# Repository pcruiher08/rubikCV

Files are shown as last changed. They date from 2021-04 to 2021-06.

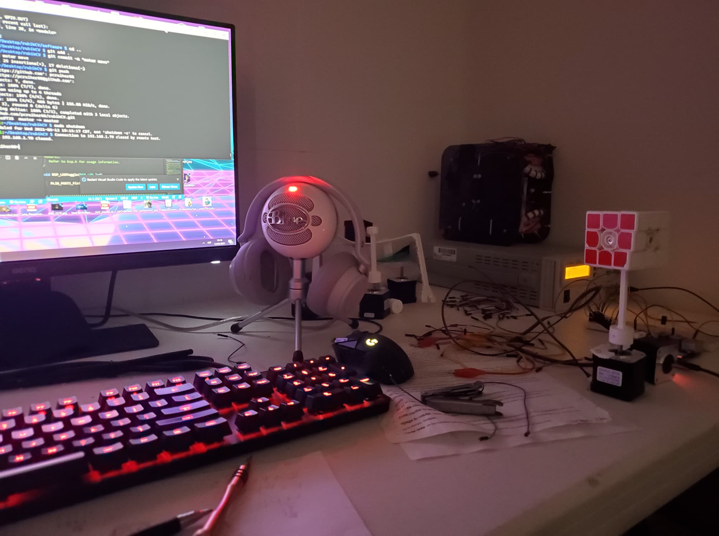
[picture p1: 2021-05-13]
journal/Day4.jpg

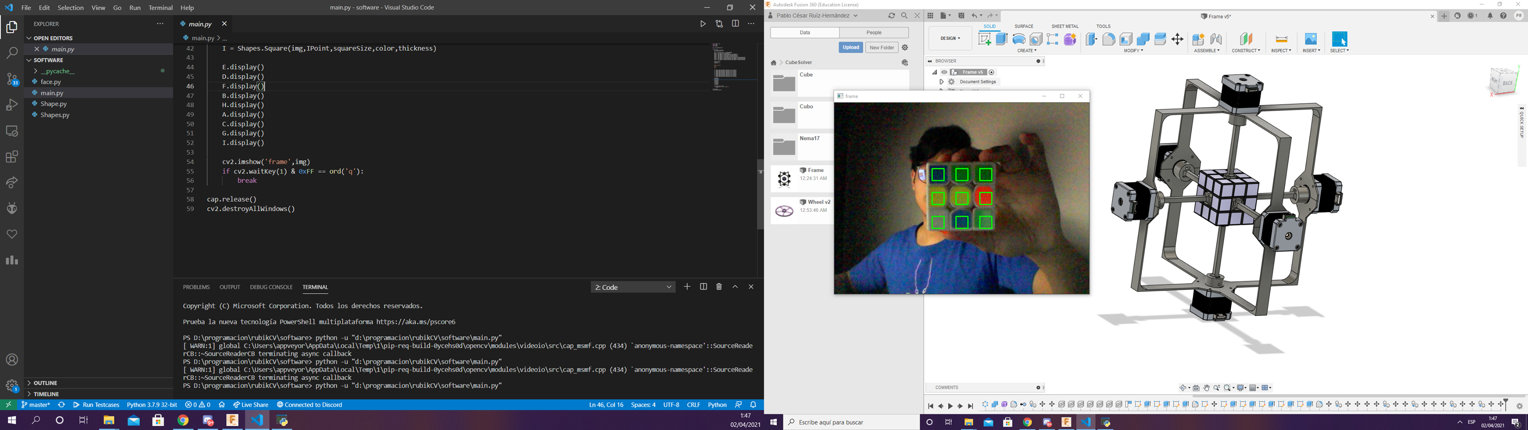
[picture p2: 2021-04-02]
journal/ssDay1.png

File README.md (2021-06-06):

# rubikCV

## Objectives

## Approach

## Development

### Mechanics
#### Brief discussion about motors
#### MoYu Weilong gts v2
#### First design (unreliable)
#### Second design (screenshots and video)
#### Screw joint design
#### Motor-Cube joints
#### 3D printing and laser cutting

### Electronics
#### Controller decision (raspberry)
#### A4988 Motor driver
#### LCD
#### 18650 lithium batteries
#### LEDs
#### Arduino with LEDs and how it would be implemented on the raspberry (level shifter)
#### Brief disccussion about the pcb and the breadboard
#### WebCam

### Software

#### OpenCV justification
* Image processing (5 pictures per face)
* Arucos (Augmented reality and geometry functions)
* HSV
* Dominant Color algorithm
#### Cube map (diagrams, polygon class)
#### States machine (scanning phase with pre defined movements)
#### Kociemba
#### Motor movement (parser, motor class, motor speed)
#### LEDs
#### LCD (LCD class)

## Results

## Improvements

## Conlusions

## DIY

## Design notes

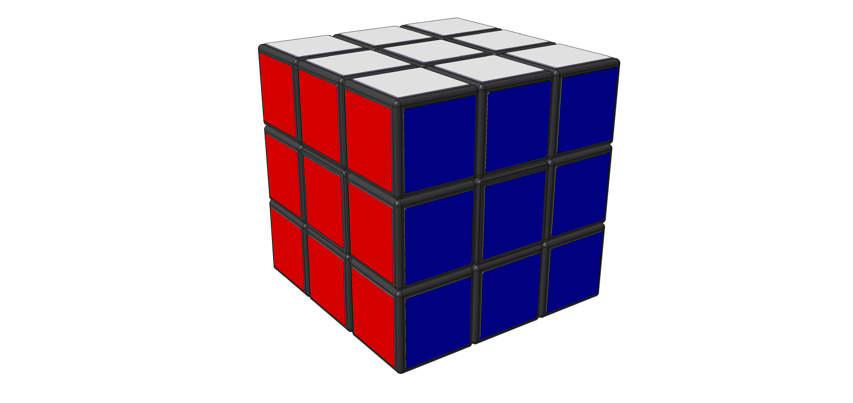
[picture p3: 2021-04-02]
hardware/CAD/cube/RubiksCube.jpg

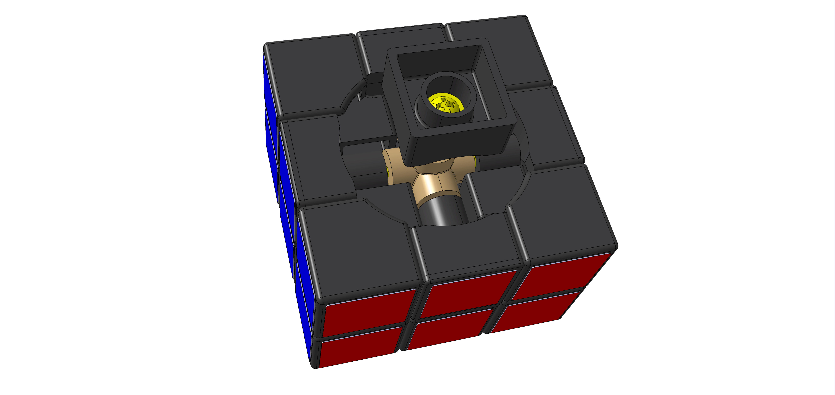
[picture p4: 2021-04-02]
hardware/CAD/cube/RubiksCube2.jpg

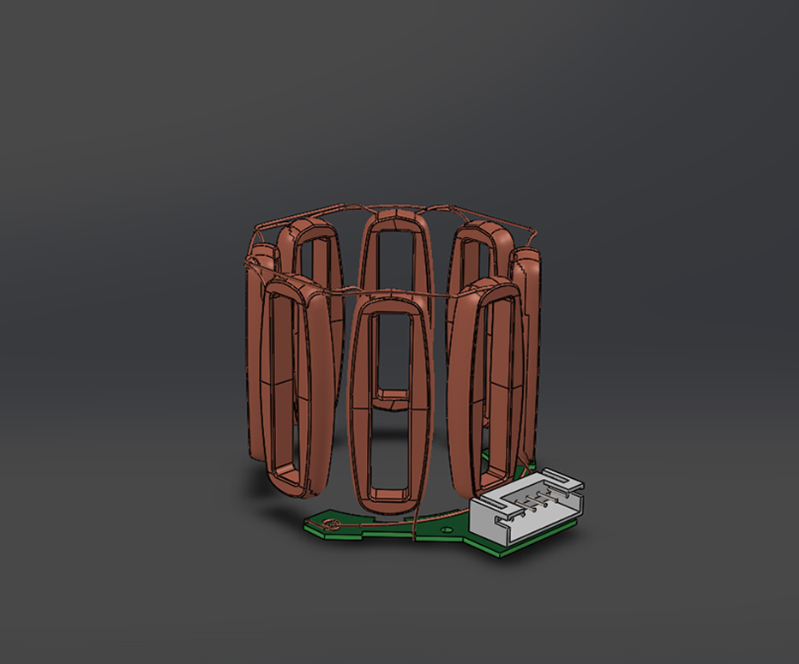
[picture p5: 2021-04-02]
hardware/CAD/nema17/Electronics.jpg

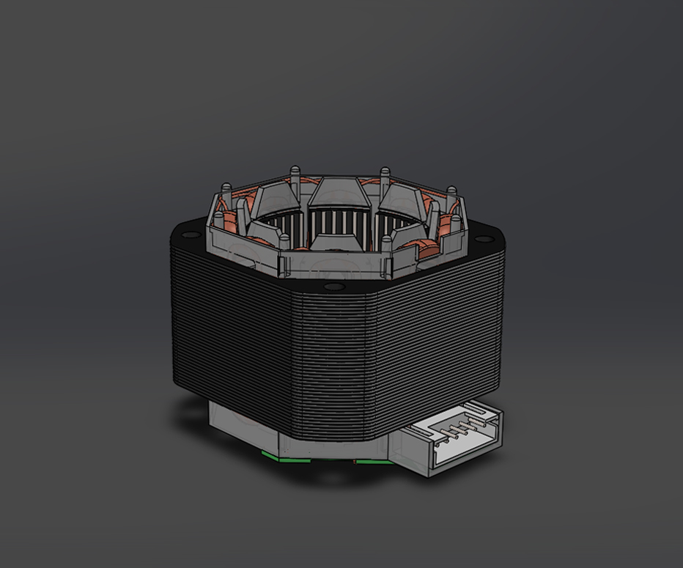
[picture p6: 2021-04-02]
hardware/CAD/nema17/Stator.jpg

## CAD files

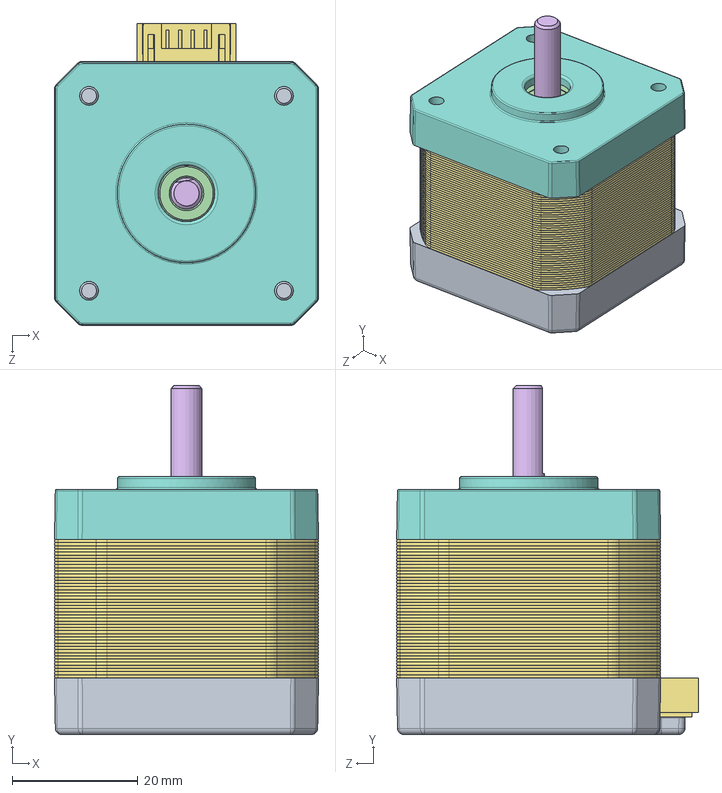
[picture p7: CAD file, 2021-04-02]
hardware/CAD/nema17/Nema17.SLDASM
42.0 x 55.5 x 48.0 mm
Bottom_cap
Protective_film_bottom
Bearing_spring
Bearing x 2
Thick_washer x 2
Rotor
Stator
Top_cap
Screw x 4

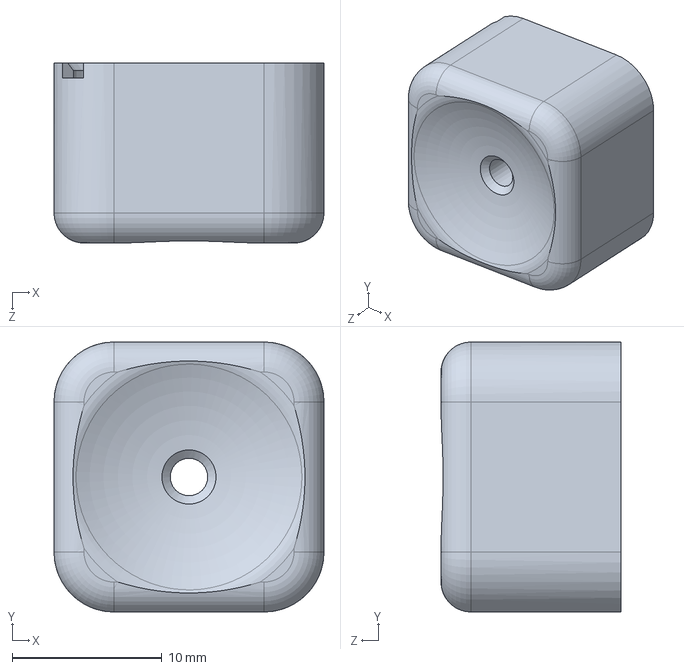
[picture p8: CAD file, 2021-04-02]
hardware/CAD/3x3 mk1/centre.SLDPRT
18.0 x 18.0 x 12.0 mm

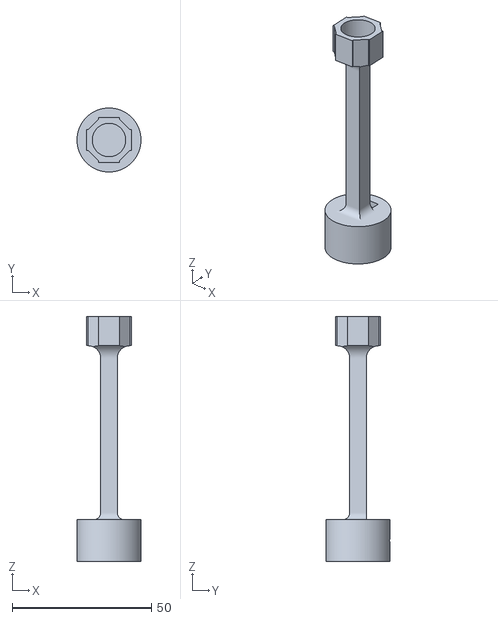
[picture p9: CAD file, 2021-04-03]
hardware/CAD/Body12.stl
23.0 x 23.0 x 88.0

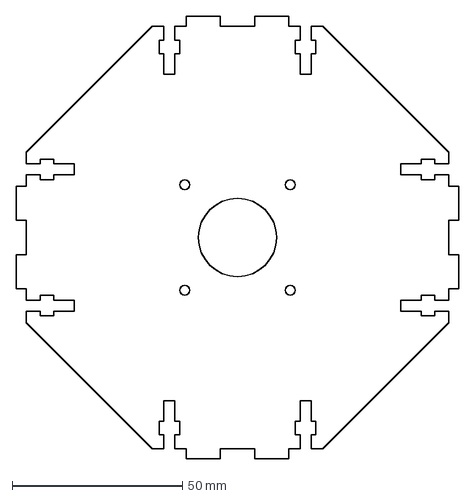
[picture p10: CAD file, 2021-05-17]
hardware/CAD/Corte Laser/tapa.dxf
130.0 x 130.0 mm

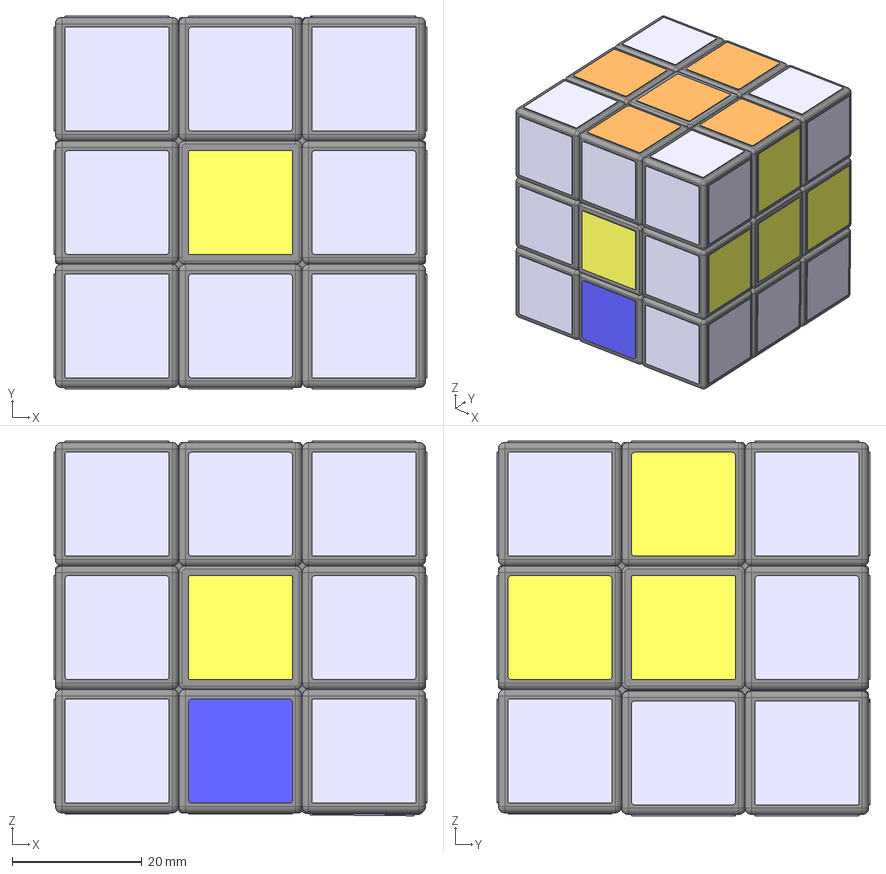
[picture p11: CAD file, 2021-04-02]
hardware/CAD/cube/RubiksCube.stp
57.4 x 57.4 x 57.7 mm
Cross
Center x 6
Edge x 12
Corner x 8
Cup x 6
Spring x 6
Coloring

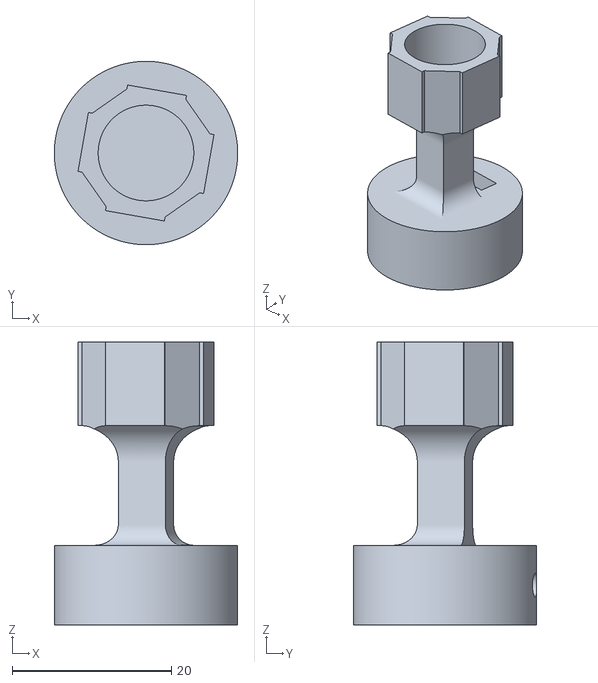
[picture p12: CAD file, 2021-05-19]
hardware/CAD/Impresion 3D/jointv1.stl
23.0 x 23.0 x 35.5

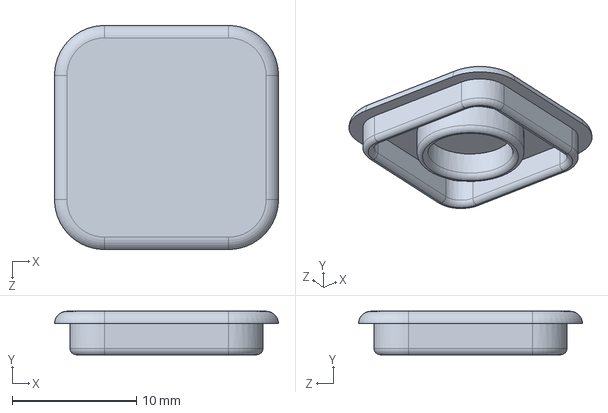
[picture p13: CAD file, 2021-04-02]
hardware/CAD/3x3 mk1/Cap.SLDPRT
18.0 x 3.50 x 18.0 mm

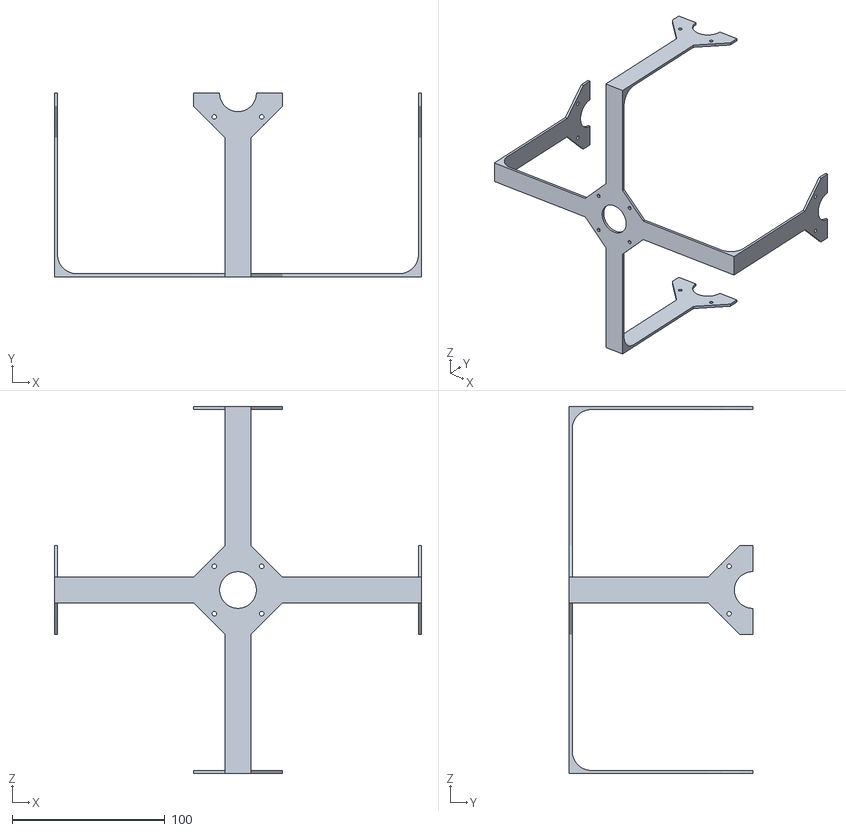
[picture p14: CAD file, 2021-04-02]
hardware/CAD/Body2.stl
240.0 x 120.0 x 240.0

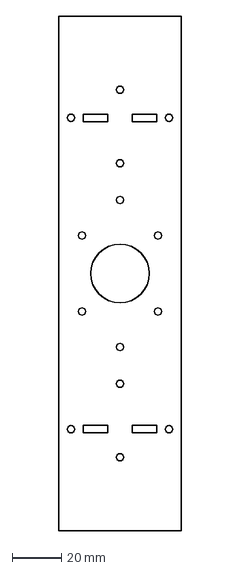
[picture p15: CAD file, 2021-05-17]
hardware/CAD/Corte Laser/columna.dxf
50.0 x 210.0 mm

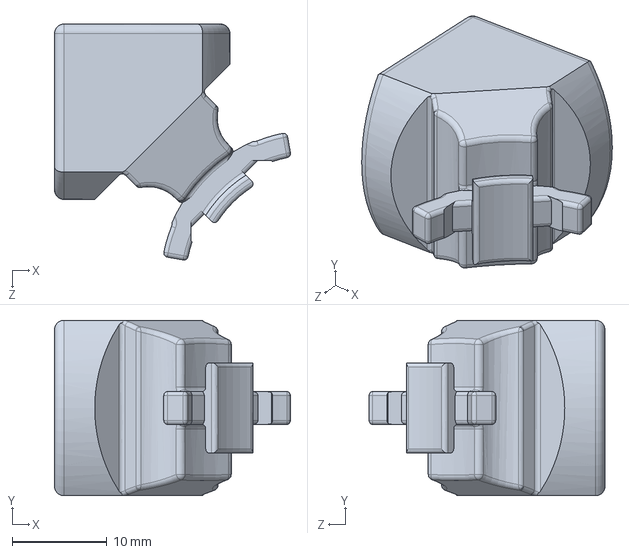
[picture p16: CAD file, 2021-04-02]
hardware/CAD/3x3 mk1/Edge.SLDPRT
24.9 x 18.5 x 24.9 mm

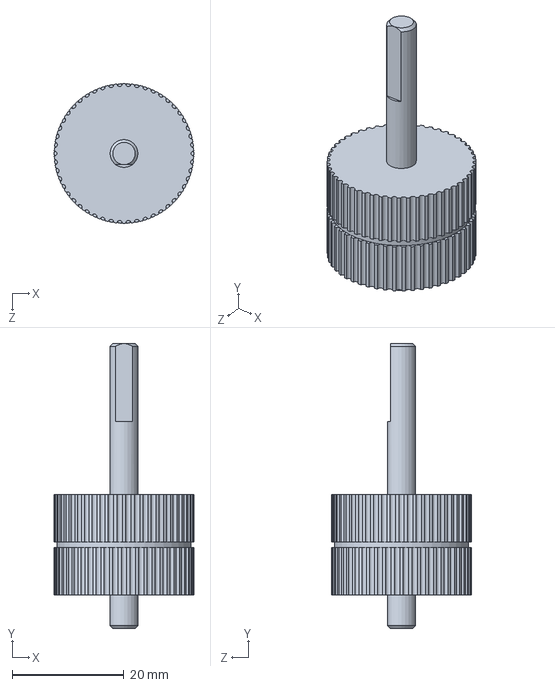
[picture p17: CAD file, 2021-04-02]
hardware/CAD/nema17/Rotor.SLDPRT
25.0 x 51.0 x 25.0 mm

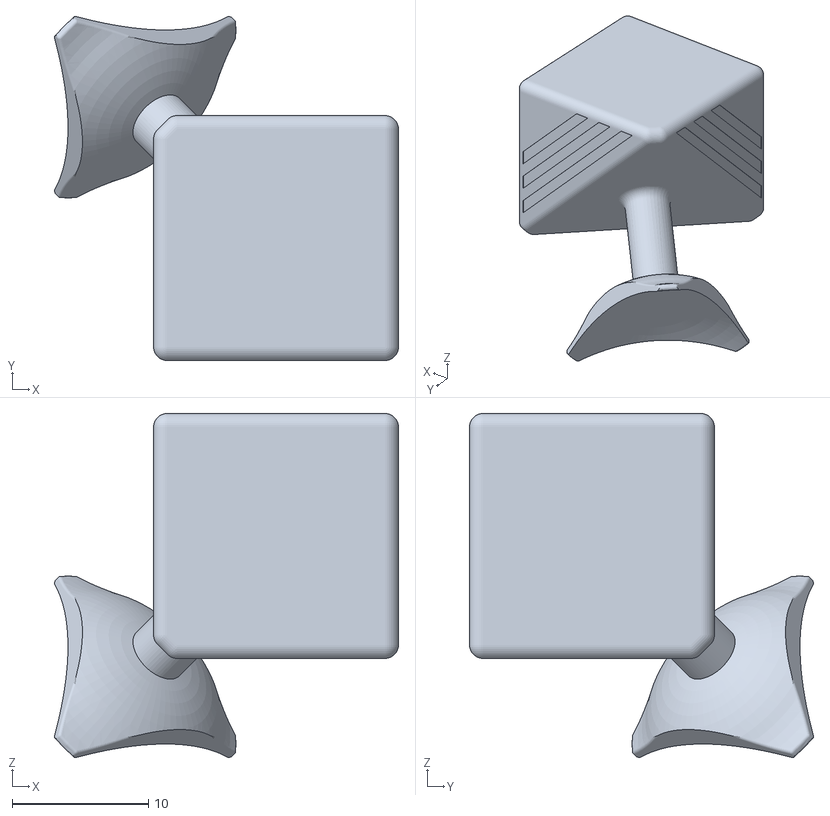
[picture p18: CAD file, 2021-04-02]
hardware/CAD/3x3 mk1/corner.STL
25.3 x 25.3 x 25.3

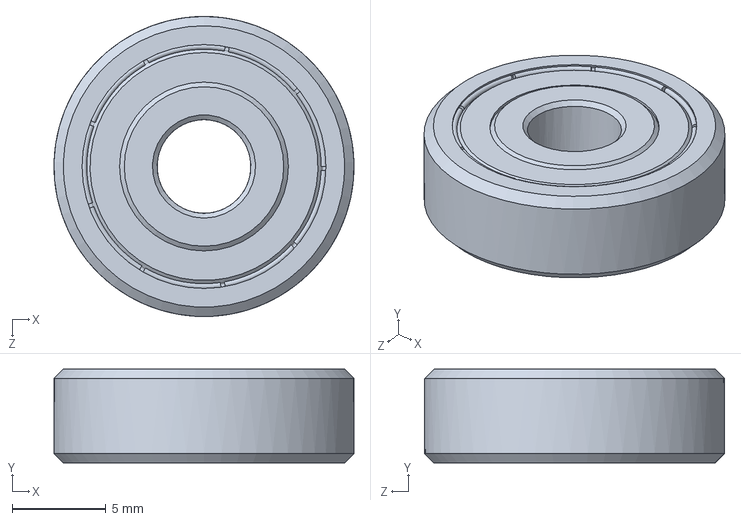
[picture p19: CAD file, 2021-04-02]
hardware/CAD/nema17/Bearing.SLDPRT
16.0 x 5.00 x 16.0 mm

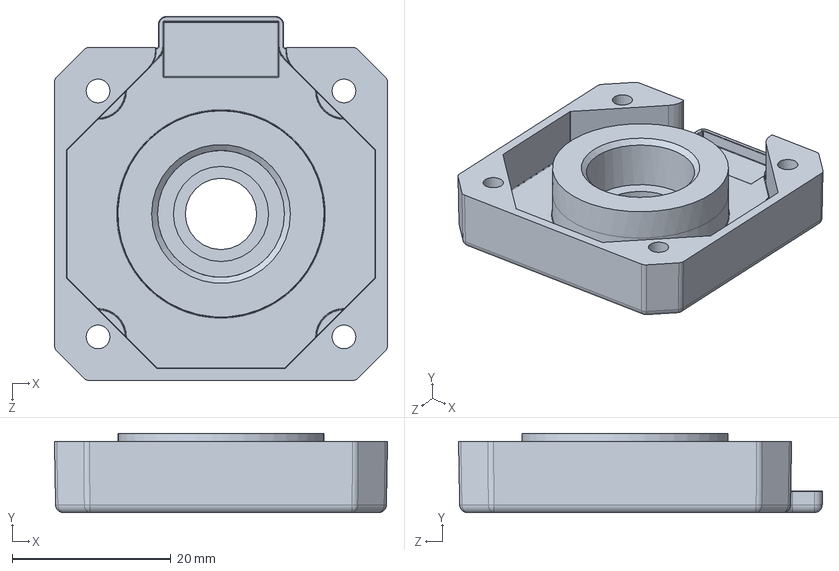
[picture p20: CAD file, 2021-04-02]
hardware/CAD/nema17/Bottom_cap.SLDPRT
42.0 x 10.0 x 45.9 mm

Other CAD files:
hardware/CAD/3x3 mk1/corner post cut.SLDPRT
hardware/CAD/nema17/Bearing_spring.SLDPRT
hardware/CAD/nema17/Top_cap.SLDPRT
hardware/CAD/nema17/Protective_film_bottom.SLDPRT
hardware/CAD/3x3 mk1/Cap.STL
hardware/CAD/3x3 mk1/Edge.STL
hardware/CAD/3x3 mk1/centre.STL
hardware/CAD/nema17/Screw.SLDPRT
hardware/CAD/nema17/Thick_washer.SLDPRT

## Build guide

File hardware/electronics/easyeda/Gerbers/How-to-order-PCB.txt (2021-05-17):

How to Order PCB

Please refer to:
https://docs.easyeda.com/en/PCB/Order-PCB

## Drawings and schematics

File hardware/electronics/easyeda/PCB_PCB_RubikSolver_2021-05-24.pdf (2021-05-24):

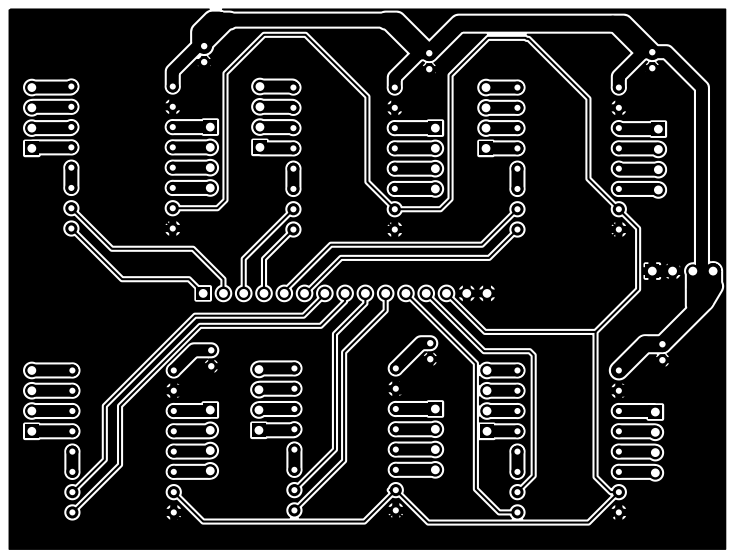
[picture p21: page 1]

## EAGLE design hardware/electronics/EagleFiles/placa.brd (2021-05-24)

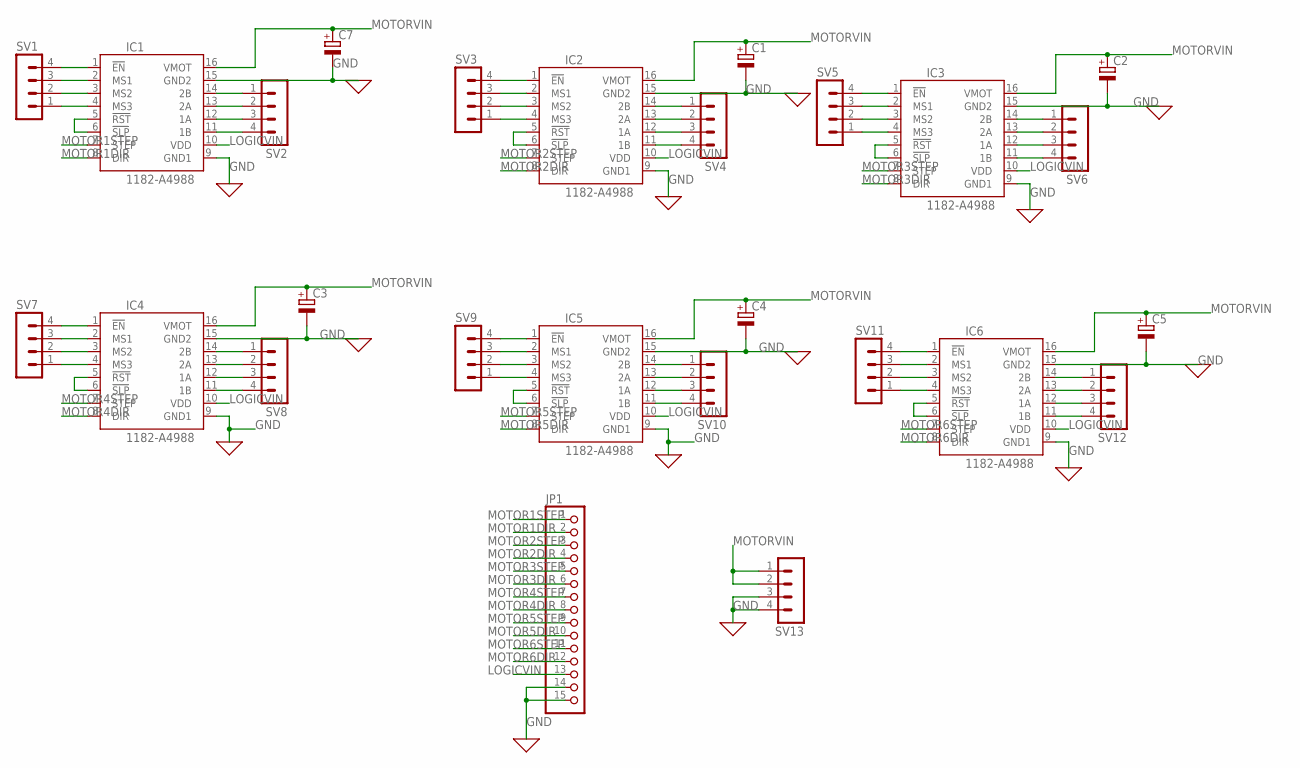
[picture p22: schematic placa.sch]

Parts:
C1, C2, C3, C4, C5, C7: CPOL-EUE2.5-7; E2,5-7
IC1, IC2, IC3, IC4, IC5, IC6: 1182-A4988; A4988
JP1: PINHD-1X15; 1X15
SV1, SV2, SV3, SV4, SV5, SV6, SV7, SV8, SV9, SV10, SV11, SV12, SV13: MA04-1

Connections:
GND: C1.-, C2.-, C3.-, C4.-, C5.-, C7.-, IC1.9 (GND1), IC1.15 (GND2), IC2.9 (GND1), IC2.15 (GND2), IC3.9 (GND1), IC3.15 (GND2), IC4.9 (GND1), IC4.15 (GND2), IC5.9 (GND1), IC5.15 (GND2), IC6.9 (GND1), IC6.15 (GND2), JP1.14, JP1.15, SV13.3, SV13.4
LOGICVIN: IC1.10 (VDD), IC2.10 (VDD), IC3.10 (VDD), IC4.10 (VDD), IC5.10 (VDD), IC6.10 (VDD), JP1.13
MOTOR1DIR: IC1.8 (DIR), JP1.2
MOTOR1STEP: IC1.7 (STEP), JP1.1
MOTOR2DIR: IC2.8 (DIR), JP1.4
MOTOR2STEP: IC2.7 (STEP), JP1.3
MOTOR3DIR: IC3.8 (DIR), JP1.6
MOTOR3STEP: IC3.7 (STEP), JP1.5
MOTOR4DIR: IC4.8 (DIR), JP1.8
MOTOR4STEP: IC4.7 (STEP), JP1.7
MOTOR5DIR: IC5.8 (DIR), JP1.10
MOTOR5STEP: IC5.7 (STEP), JP1.9
MOTOR6DIR: IC6.8 (DIR), JP1.12
MOTOR6STEP: IC6.7 (STEP), JP1.11
MOTORVIN: C1.+, C2.+, C3.+, C4.+, C5.+, C7.+, IC1.16 (VMOT), IC2.16 (VMOT), IC3.16 (VMOT), IC4.16 (VMOT), IC5.16 (VMOT), IC6.16 (VMOT), SV13.1, SV13.2
unnamed: IC1.1 (!EN), SV1.4
unnamed: IC1.2 (MS1), SV1.3
unnamed: IC1.3 (MS2), SV1.2
unnamed: IC1.4 (MS3), SV1.1
unnamed: IC1.5 (!RST), IC1.6 (!SLP)
unnamed: IC2.1 (!EN), SV3.4
unnamed: IC2.2 (MS1), SV3.3
unnamed: IC2.3 (MS2), SV3.2
unnamed: IC1.14 (2B), SV2.1
unnamed: IC1.13 (2A), SV2.2
unnamed: IC1.12 (1A), SV2.3
unnamed: IC1.11 (1B), SV2.4
unnamed: IC2.4 (MS3), SV3.1
unnamed: IC2.5 (!RST), IC2.6 (!SLP)
unnamed: IC2.14 (2B), SV4.1
unnamed: IC2.13 (2A), SV4.2
unnamed: IC2.12 (1A), SV4.3
unnamed: IC2.11 (1B), SV4.4
unnamed: IC3.1 (!EN), SV5.4
unnamed: IC3.2 (MS1), SV5.3
unnamed: IC3.3 (MS2), SV5.2
unnamed: IC3.4 (MS3), SV5.1
unnamed: IC3.5 (!RST), IC3.6 (!SLP)
unnamed: IC3.14 (2B), SV6.1
unnamed: IC3.13 (2A), SV6.2
unnamed: IC3.12 (1A), SV6.3
unnamed: IC3.11 (1B), SV6.4
unnamed: IC4.1 (!EN), SV7.4
unnamed: IC4.2 (MS1), SV7.3
unnamed: IC4.3 (MS2), SV7.2
unnamed: IC4.4 (MS3), SV7.1
unnamed: IC4.5 (!RST), IC4.6 (!SLP)
unnamed: IC4.14 (2B), SV8.1
unnamed: IC4.13 (2A), SV8.2
unnamed: IC4.12 (1A), SV8.3
unnamed: IC4.11 (1B), SV8.4
unnamed: IC5.1 (!EN), SV9.4
unnamed: IC5.2 (MS1), SV9.3
unnamed: IC5.3 (MS2), SV9.2
unnamed: IC5.4 (MS3), SV9.1
unnamed: IC5.5 (!RST), IC5.6 (!SLP)
unnamed: IC5.14 (2B), SV10.1
unnamed: IC5.13 (2A), SV10.2
unnamed: IC5.12 (1A), SV10.3
unnamed: IC5.11 (1B), SV10.4
unnamed: IC6.1 (!EN), SV11.4
unnamed: IC6.2 (MS1), SV11.3
unnamed: IC6.3 (MS2), SV11.2
unnamed: IC6.4 (MS3), SV11.1
unnamed: IC6.5 (!RST), IC6.6 (!SLP)
unnamed: IC6.14 (2B), SV12.1
unnamed: IC6.13 (2A), SV12.2
unnamed: IC6.12 (1A), SV12.3
unnamed: IC6.11 (1B), SV12.4

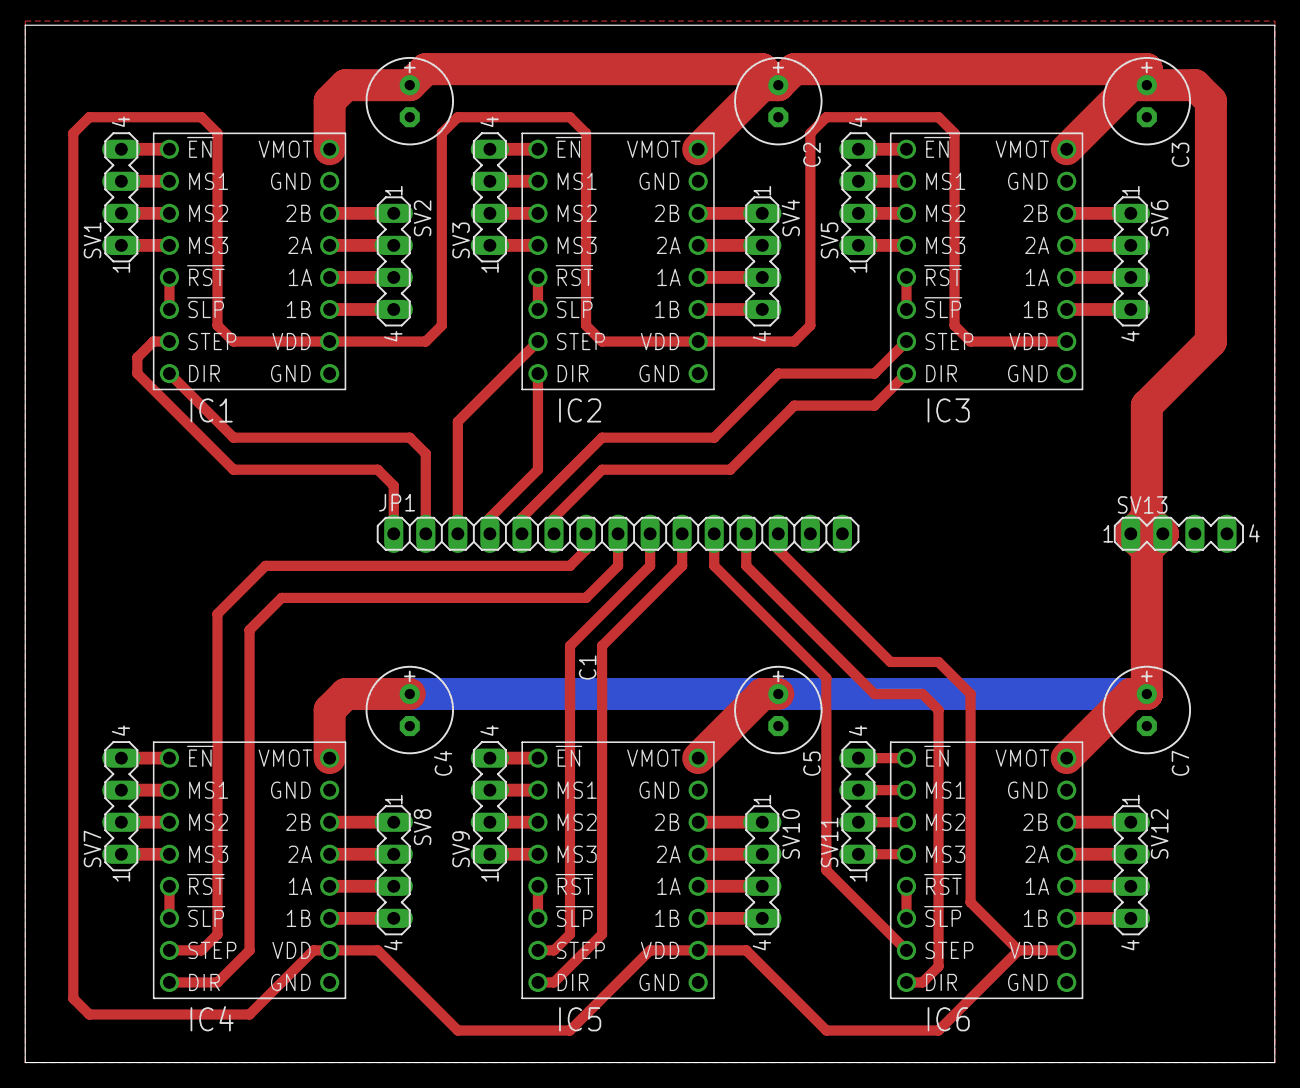
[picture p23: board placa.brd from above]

Board: 2 copper layers, 99.0 x 82.2 mm, 26 parts (0 on the bottom side), 69 nets.

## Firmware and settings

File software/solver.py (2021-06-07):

import cv2
import cv2.aruco as aruco
import numpy as np
import os
from polygon import Polygon 
import math as m 
import LCD
from motor import Motor
import kociemba

def commandParser(series):
    #se recibe un string en formato R U R’ U R U2 R’ U
    movements = series.split(' ')
    for move in movements:
        twoMoves = False
        directionFlag = False
        if len(move) == 2:
            if(move[1] == '2'):
                #cw cw
                twoMoves = True
            else:
                #ccw
                directionFlag = True

        if(move[0] == 'F'):
            if(twoMoves):
                F.turn90CW()
                F.turn90CW()
            else:
                F.turn90(directionFlag)
        if(move[0] == 'L'):
            if(twoMoves):
                L.turn90CW()
                L.turn90CW()
            else:
                L.turn90(directionFlag)  
        if(move[0] == 'R'):
            if(twoMoves):
                R.turn90CW()
                R.turn90CW()
            else:
                R.turn90(directionFlag)
        if(move[0] == 'B'):
            if(twoMoves):
                B.turn90CW()
                B.turn90CW()
            else:
                B.turn90(directionFlag)
        if(move[0] == 'U'):
            if(twoMoves):
                U.turn90CW()
                U.turn90CW()
            else:
                U.turn90(directionFlag)
        if(move[0] == 'D'):
            if(twoMoves):
                D.turn90CW()
                D.turn90CW()
            else:
                D.turn90(directionFlag)
        twoMoves = False
        directionFlag = False


def getMidPoint(a, b):
    return (int((a[0] + b[0]) / 2), int((a[1] + b[1]) / 2))

def getThirdPoint(a, b):
    return (int((a[0] + b[0]) / 3), int((a[1] + b[1]) / 3))

def getTwoThirdsPoint(a, b):
    return (int((a[0] + b[0]) * 2 / 3), int((a[1] + b[1]) * 2 / 3))

def getFractionPoint(a, b, t):
    return ( int(a[0] * (1 - t) ) + int(b[0] * t), int( a[1] * (1 - t) ) + int(b[1] * t) )

def distancePointPoint(a, b):
    return int( m.sqrt( (a[0] - b[0]) * (a[0] - b[0]) + (a[1] - b[1]) * (a[1] - b[1]) ) )

def pointInterceptPointPointPointPoint(a, b, c, d):

    divide = (a[0] - b[0]) * (c[1] - d[1]) - (a[1] - b[1]) * (c[0] - d[0])
    punto1 = ((a[0]*b[1] - a[1]*b[0]) * (c[0]-d[0]) - (a[0]-b[0]) * (c[0]*d[1] - c[1]*d[0]))/divide
    punto2 = ((a[0]*b[1] - a[1]*b[0]) * (c[1]-d[1]) - (a[1]-b[1]) * (c[0]*d[1] - c[1]*d[0]))/divide
    return (int(punto1), int(punto2))

def calculateHSVDistance(a, b):
    dh = min(abs(b[0]-a[0]), 360-abs(b[0]-a[0])) / 180.0
    ds = abs(b[1]-a[1])
    dv = abs(b[2]-b[0]) / 255.0
    return m.sqrt(dh*dh+ds*ds+dv*dv)

def namestr(obj, namespace):
    return [name for name in namespace if namespace[name] is obj]

def pointInsidePolygon(point, polygon):
    isInsideRight = True
    isInsideLeft = True
    #print("estoy checando ", polygon, "con ", point)
    for i in range(len(polygon)):
        result = (point[1] - polygon[i][1]) * (polygon[(i + 1) % len(polygon)][0] - polygon[i][0]) - (point[0] - polygon[i][0]) * (polygon[(i + 1) % len(polygon)][1] - polygon[i][1])
        if(not (result < 0)):
            isInsideRight = False

    for i in range(len(polygon)):
        result = (point[1] - polygon[i][1]) * (polygon[(i + 1) % len(polygon)][0] - polygon[i][0]) - (point[0] - polygon[i][0]) * (polygon[(i + 1) % len(polygon)][1] - polygon[i][1])
        if(not (result > 0)):
            isInsideLeft = False

    return isInsideRight or isInsideLeft


def findArucoMarkers(img, markerSize = 4, totalMarkers=250, draw=True):
    gray = cv2.cvtColor(img, cv2.COLOR_BGR2GRAY)
    key = getattr(aruco, f'DICT_{markerSize}X{markerSize}_{totalMarkers}')
    arucoDict = aruco.Dictionary_get(key)
    arucoParam = aruco.DetectorParameters_create()
    corners, ids, rejected = aruco.detectMarkers(gray, arucoDict, parameters = arucoParam)
    # print(ids)
    if draw:
        aruco.drawDetectedMarkers(img, corners,ids) 
    return [corners, ids]


def drawPolygons(img, overlay, polygons):
    for polygon in polygons:
        polygon.paintPolygonLines(img)
        polygon.fillPolygon(img, overlay)


def colorFinder(img, contours, color_ranges_HSV):
    contoursSpecial = contours.copy()
    hsv = cv2.cvtColor(img, cv2.COLOR_BGR2HSV)
    edgee = cv2.cvtColor(img, cv2.COLOR_BGR2BGRA)
    #cv2.imshow('1', img)

    edge = cv2.Canny(edgee,100,200)
    #cv2.imshow("e",edge)

    rows,cols,dim = img.shape
    out = np.zeros([rows, cols, dim], dtype=np.uint8)
    acumm = mask = np.zeros((rows, cols), dtype=np.uint8)

    low_red = np.array([0,50,50])
    upper_red = np.array([10,255,255])


    contoursFinal = []
    colors = ['A','A','A','A','A','A','A','A','A','A','A','A','A','A','A']
    maskTemp = np.zeros([rows,cols,3],np.uint8)
    for i in range(len(contoursSpecial)):
        xavg = 0
        yavg = 0
        for j in range(len(contoursSpecial[i][0])):
            xavg += contoursSpecial[i][0][j][1]
            yavg += contoursSpecial[i][0][j][0]
        xavg /= len(contoursSpecial[i][0])
        yavg /= len(contoursSpecial[i][0])
        xavg = int(xavg)
        yavg = int(yavg)
        mask = np.zeros([rows,cols],np.uint8)
        mask[xavg][yavg] = 255
        '''
        mask[xavg+1][yavg] = 255
        mask[xavg][yavg+1] = 255
        mask[xavg-1][yavg] = 255
        mask[xavg][yavg-1] = 255
        mask[xavg+1][yavg+1] = 255
        mask[xavg-1][yavg-1] = 255
        mask[xavg+1][yavg-1] = 255
        mask[xavg-1][yavg+1] = 255
        '''
        #cv2.drawContours(mask,contoursSpecial[i],-1,255,-1)
        mean = cv2.mean(hsv,mask=mask)
        temp = np.zeros([1,1,3],np.uint8)
        temp[0][0] = mean[:3]
        #print(mean)
        #cv2.drawContours(img,contoursSpecial[i],-1,[0,0,255],3)
        #cv2.drawContours(img,[aprox],-1,mean[:2],3)
        #cv2.fillPoly(img,pts = [aprox], color = mean)
        for k in range(len(color_ranges_HSV)):
            inR = cv2.inRange(temp,color_ranges_HSV[k][1],color_ranges_HSV[k][0])
            if(inR[0][0] == 255):
                #cv2.drawContours(maskTemp,[aprox],-1,mean,3)
                #contoursFinal.append([contoursSpecial[i],color_ranges_HSV[k][2]])
                colors[i] = color_ranges_HSV[k][2]
                cv2.fillPoly(maskTemp,pts = contoursSpecial[i], color = color_ranges_HSV[k][3])

    return colors


def arucoProcessing(img):
    contoursSpecial = []
    arucofound = findArucoMarkers(img)
    howManyArucos = len(arucofound[0])
    encontreDosArucos = False
    if howManyArucos!=0:
        coordinates = []
        for bbox, id in zip(arucofound[0], arucofound[1]):
            #print(bbox, id)
            coords = tuple(bbox[0][0])
            #print(coords)
            coordinates.append(coords)
            #img = cv2.circle(img, coords, 2, redColor, 5)
        if(howManyArucos == 2):
            encontreDosArucos = True
            topCorner = getMidPoint(coordinates[0], coordinates[1])
            topCorner = (topCorner[0]-5, topCorner[1]+22)
            bottomCorner = (topCorner[0]-5, topCorner[1]+170)
            rightCorner = (bottomCorner[0]+125, bottomCorner[1]+40)
            leftCorner = (bottomCorner[0]-120, bottomCorner[1]+37)

            bigLine = 3
            smallLine = 3
            #central line
            img = cv2.line(img, topCorner, bottomCorner,[0,0,0],bigLine)
            #right line
            img = cv2.line(img, bottomCorner, rightCorner,[0,0,0],bigLine)
            #left line
            img = cv2.line(img, bottomCorner, leftCorner,[0,0,0],bigLine)

            P1 = leftCorner
            P2 = getFractionPoint(bottomCorner, leftCorner, 2/3)
            P3 = getFractionPoint(bottomCorner, leftCorner, 1/3)
            P4 = bottomCorner
            P5 = getFractionPoint(bottomCorner, topCorner, 1/3+0.05) 
            P6 = getFractionPoint(bottomCorner, topCorner, 2/3+0.05)
            P7 = topCorner
            P8 = getFractionPoint(bottomCorner, rightCorner, 1/3 + 0.05)
            P9 = getFractionPoint(bottomCorner, rightCorner, 2/3 + 0.05)
            P10 = rightCorner 
            P11 = (P1[0]+8, P1[1] - distancePointPoint(P4, P5)+10) 
            P12 = getFractionPoint(P11, P5, 1/3)
            P15 = (P3[0]+7, P3[1] - distancePointPoint(bottomCorner, topCorner)+7)
            P13 = pointInterceptPointPointPointPoint(P3,P15,P5,P11)
            P14 = getFractionPoint(P15, P3, 1/3 - 0.05)
            P16 = (P8[0] + 2, P8[1] - distancePointPoint(topCorner, bottomCorner) + 5)
            P17 = getFractionPoint(P16, P8, 1/3 - 0.05)
            P20 = (P5[0] + distancePointPoint(bottomCorner, rightCorner) - 10, P5[1] + distancePointPoint(P5, P4) - 13)
            P18 = pointInterceptPointPointPointPoint(P8,P16,P5,P20)
            P19 = getFractionPoint(P5, P20, 2/3 + 0.08)
            P21 = (P1[0] + distancePointPoint(P4,P5)-7, P1[1] + 16)
            P22 = getFractionPoint(P21, P8, 1/3-0.05)
            P25 = (P10[0]-35, P1[1]+20)
            P23 = pointInterceptPointPointPointPoint(P3,P25,P8,P21)
            P24 = getFractionPoint(P25, P3, 1/3)


            C1C = [np.array([P1,P11,P12,P2])]
            C2C = [np.array([P2, P12, P13, P3])]
            C3C = [np.array([P3, P13, P5, P4])]
            C4C = [np.array([P4, P5, P18, P8])]
            C5C = [np.array([P8, P18, P19, P9])]
            C6C = [np.array([P9, P19, P20, P10])]
            C7C = [np.array([P13, P14, P6, P5])]
            C8C = [np.array([P14, P15, P7, P6])]
            C9C = [np.array([P6, P7, P16, P17])]
            C10C = [np.array([P5, P6, P17, P18])]
            C11C = [np.array([P21, P1, P2, P22])]
            C12C = [np.array([P22, P2, P3, P23])]
            C13C = [np.array([P23, P3, P4, P8])]
            C14C = [np.array([P23, P8, P9, P24])]
            C15C = [np.array([P24, P9, P10, P25])]

            contoursSpecial = [C1C,C2C,C3C,C4C,C5C,C6C,C7C,C8C,C9C,C10C,C11C,C12C,C13C,C14C,C15C]


            #lineas especiales
            
            img = cv2.line(img, P5, P20,[0,0,0],smallLine)
            img = cv2.line(img, P8, P16,[0,0,0],smallLine)
            img = cv2.line(img, P10, P20,[0,0,0],smallLine)
            img = cv2.line(img, P7, P16,[0,0,0],smallLine)
            img = cv2.line(img, P6, P17,[0,0,0],smallLine)
            img = cv2.line(img, P9, P19,[0,0,0],smallLine)
            img = cv2.line(img, P3, P15,[0,0,0],smallLine)
            img = cv2.line(img, P5, P11,[0,0,0],smallLine)
            img = cv2.line(img, P1, P11,[0,0,0],smallLine)
            img = cv2.line(img, P15, P7,[0,0,0],smallLine)
            img = cv2.line(img, P6, P14,[0,0,0],smallLine)
            img = cv2.line(img, P2, P12,[0,0,0],smallLine)
            img = cv2.line(img, P8, P21,[0,0,0],smallLine)
            img = cv2.line(img, P3, P25,[0,0,0],smallLine)
            img = cv2.line(img, P10, P25,[0,0,0],smallLine)
            img = cv2.line(img, P1, P21,[0,0,0],smallLine)
            img = cv2.line(img, P2, P22,[0,0,0],smallLine)
            img = cv2.line(img, P9, P24,[0,0,0],smallLine)
    return contoursSpecial
    
def dominantColor(colorsArr):
    result = ['A','A','A','A','A','A','A','A','A','A','A','A','A','A','A']
    result2 = ['A','A','A','A','A','A','A','A','A','A','A','A','A','A','A']
    kociembaMap = {'B' : 'F', 'O': 'L', 'R' : 'R', 'G' : 'B', 'W' : 'D', 'Y': 'U'}
    for i in range(len(colorsArr[0])):
        colors = {'W' : 0, 'O' : 0, 'G' : 0, 'R' : 0, 'Y' : 0, 'B' : 0}
        max = -1
        maxL = 'A'
        for j in range(len(colorsArr)):
            colors[colorsArr[j][i]] += 1
            if(colors[colorsArr[j][i]] > max):
                max = colors[colorsArr[j][i]]
                maxL = colorsArr[j][i]
            result[i] = kociembaMap[maxL]
            result2[i] = maxL
    return result, result2

def stringParser(string):
    newString = ''
    kociembaMap = {'F' : 'B', 'L': 'O', 'R' : 'R', 'B' : 'G', 'D' : 'W', 'U': 'Y'}
    for color in string:
        newString += kociembaMap[color]
    return newString

def printAsMatrix(string, n, m):
    newString = stringParser(string)
    for i in range(n):
        for j in range(m):
            print(newString[i * m + j], end = ' ')
        print('\n')
    print('\n')

cap = cv2.VideoCapture(0)   
greenColor = (0,255,0)
blueColor = (255,0,0)
redColor = (0,0,255)


color_ranges_HSV = [
    [(179, 59, 255), (0, 0, 106),"W",(0,0,255)],
    [(180, 255, 255), (159, 50, 70),"R",(4,255,255)],
    [(8, 255, 255), (0, 45, 0),"R",(4,255,255)],
    [(20, 209, 255), (8, 58, 33),"O",(19,255,255)],
    [(35, 255, 255), (25, 50, 70),"Y",(30,255,255)],
    [(120, 255, 255), (90, 90, 135),"B",(120,255,255)],
    [(89, 255, 255), (36, 50, 70),"G",(60,255,255)]
]


stagePictures = []
matrizKociemba = []

scanState = 0
turnDelay = .005 / 8 * 1/2

F = Motor(26,19)
L = Motor(13,6)
R = Motor(21, 20)
B = Motor(16,12)
U = Motor(5, 22)
D = Motor(27, 17)

screen = LCD.lcd()
screen.lcd_clear()
screen.lcd_display_string("hay 6 motores", 1)

F.setDelay(turnDelay)
L.setDelay(turnDelay)
R.setDelay(turnDelay)
B.setDelay(turnDelay)
U.setDelay(turnDelay)
D.setDelay(turnDelay)

'''
estado 0, esperar 5 ticks para estabilizacion
estado 1, foto y agregar al array y luego mover motores para transicion al estado 2
estado 2, foto y agregar al array y luego mover motores para transicion al estado 3
estado 3, foto y agregar al array y luego mover motores para transicion al estado 4
estado 4, foto y agregar al array y luego mover motores para transicion al estado 5
estado 5, foto y agregar al array y luego mover motores para transicion al estado 6
estado 6, foto y agregar al array y luego mover motores para transicion al estado 7
estado 7, foto y agregar al array y luego mover motores para transicion al estado 8
estado 8, foto y agregar al array y luego mover motores para transicion al estado 9
estado 9, foto y agregar al array y luego mover motores para transicion al estado 10
estado 10, foto y agregar al array y luego mover motores para transicion al estado 11
estado 11, kociemba y motores
'''
screen = LCD.lcd()
screen.lcd_clear()
estadoActual = 0
ticks = 0
while True:
    success, img = cap.read()
    original = img.copy()
    #img = cv2.imread("4.jpg")
    
    contoursSpecial = arucoProcessing(img)
    respuesta = colorFinder(img, contoursSpecial, color_ranges_HSV)
    rows,cols,dim = img.shape
    maskTemp = np.zeros([rows,cols,3],np.uint8)
    for i in range(len(respuesta)):
        for j in range(len(color_ranges_HSV)):
            if(respuesta[i] == color_ranges_HSV[j][2]):
                cv2.fillPoly(maskTemp,pts = contoursSpecial[i], color = color_ranges_HSV[j][3])
    maskTemp = cv2.cvtColor(maskTemp, cv2.COLOR_HSV2BGR)
    cv2.imshow("color reconstruction",maskTemp)
    cv2.imshow("original image",original)


    if(estadoActual == 0):
        ticks += 1
        if(ticks > 5):
            estadoActual = 1
            ticks = 0
    elif(estadoActual == 1):
        if(ticks == 0):
            stagePictures.append(original.copy())
            screen.lcd_clear()
            screen.lcd_display_string("estado 1", 1)
            commandParser("F'")
            #motores
        ticks += 1
        if(ticks > 10):
            estadoActual = 2
            ticks = 0
    elif(estadoActual == 2):
        if(ticks == 0):
            stagePictures.append(original.copy())
            screen.lcd_clear()
            screen.lcd_display_string("estado 2", 1)
            commandParser("F'")
            #motores
        ticks += 1
        if(ticks > 10):
            estadoActual = 3
            ticks = 0
            
    elif(estadoActual == 3):
        if(ticks == 0):
            stagePictures.append(original.copy())
            screen.lcd_clear()
            screen.lcd_display_string("estado 3", 1)
            #motores
            commandParser("F2")
            commandParser("L")
        ticks += 1
        if(ticks > 10):
            estadoActual = 4
            ticks = 0
            
    elif(estadoActual == 4):
        if(ticks == 0):
            stagePictures.append(original.copy())
            screen.lcd_clear()
            screen.lcd_display_string("estado 4", 1)
            #motores
            commandParser("L")

        ticks += 1
        if(ticks > 10):
            estadoActual = 5
            ticks = 0
            
    elif(estadoActual == 5):
        if(ticks == 0):
            stagePictures.append(original.copy())
            screen.lcd_clear()
            screen.lcd_display_string("estado 5", 1)
            #motores
            commandParser("L' L'")
            commandParser("D2")

        ticks += 1
        if(ticks > 10):
            estadoActual = 6
            ticks = 0
            
    elif(estadoActual == 6):
        if(ticks == 0):
            stagePictures.append(original.copy())
            screen.lcd_clear()
            screen.lcd_display_string("estado 6", 1)
            #motores
            commandParser("D' D'")
            commandParser("U2")

        ticks += 1
        if(ticks > 10):
            estadoActual = 7
            ticks = 0
            
    elif(estadoActual == 7):
        if(ticks == 0):
            stagePictures.append(original.copy())
            screen.lcd_clear()
            screen.lcd_display_string("estado 7", 1)
            #motores
            commandParser("F'")

        ticks += 1
        if(ticks > 10):
            estadoActual = 8
            ticks = 0
            
    elif(estadoActual == 8):
        if(ticks == 0):
            stagePictures.append(original.copy())
            screen.lcd_clear()
            screen.lcd_display_string("estado 8", 1)
            #motores
            commandParser("F")
            commandParser("L")
        ticks += 1
        if(ticks > 10):
            estadoActual = 9
            ticks = 0
            
    elif(estadoActual == 9):
        if(ticks == 0):
            stagePictures.append(original.copy())
            screen.lcd_clear()
            screen.lcd_display_string("estado 9", 1)
            #motores
            commandParser("L'")
            commandParser("U' U'")
            commandParser("B' D")

        ticks += 1
        if(ticks > 10):
            estadoActual = 10
            ticks = 0
    elif(estadoActual == 10):
        if(ticks == 0):
            stagePictures.append(original.copy())
            screen.lcd_clear()
            screen.lcd_display_string("estado 10", 1)
            #motores
            commandParser("D' B")
        ticks += 1
        if(ticks > 10):
            estadoActual = 11
            ticks = 0        
    elif(estadoActual == 11):
        break
        
    cv2.imshow('arucos',img)

    k = cv2.waitKey(30) & 0xff
    if k == 27:
        break  

'''
for i in range(len(stagePictures)):
    cv2.imwrite("stage "+str(i + 1)+'.jpg', stagePictures[i])
'''
'''
k = cv2.waitKey(30) & 0xff
if k == 27:
    break  
'''


#sacamos el arreglo con la letra mas repetida por cada foto y lo guardamos en una matriz
finalColors = []
for i in range(len(stagePictures)):
    colorsToProcess = []
    for j in range(5):
        pictureToProcess = stagePictures[i].copy()
        contoursSpecial = arucoProcessing(pictureToProcess)
        respuesta = colorFinder(pictureToProcess, contoursSpecial, color_ranges_HSV)
        colorsToProcess.append(respuesta)
    
    finalColors.append(dominantColor(colorsToProcess)[0])
    colorsToProcess.clear()
print(finalColors)
#escribimos en la matriz kociemba
UString = finalColors[3][8] + finalColors[7][6] + finalColors[7][2] + finalColors[3][9] + 'U' + finalColors[8][9] + finalColors[1][2] + finalColors[1][6] + finalColors[1][7]
RString = finalColors[2][2] + finalColors[8][6] + finalColors[6][7] + finalColors[2][6] + 'R' + finalColors[9][11] + finalColors[2][7] + finalColors[5][1] + finalColors[5][2]
FString = finalColors[0][8] + finalColors[1][9] + finalColors[1][8] + finalColors[0][9] + 'F' + finalColors[2][9] + finalColors[0][3] + finalColors[0][4] + finalColors[0][5]
DString = finalColors[0][12] + finalColors[0][13] + finalColors[0][14] + finalColors[0][11] + 'D' + finalColors[5][11] + finalColors[0][10] + finalColors[5][13] + finalColors[5][12]
LString = finalColors[3][7] + finalColors[3][6] + finalColors[0][7] + finalColors[4][6] + 'L' + finalColors[0][6] + finalColors[0][0] + finalColors[0][1] + finalColors[0][2]
BString =  finalColors[6][8] + finalColors[7][9] + finalColors[4][3] +  finalColors[9][1] + 'B' +  finalColors[4][9] +  finalColors[5][3] + finalColors[5][4] + finalColors[4][8]

KociembaString = UString + RString + FString + DString + LString + BString

print("YELLOW")
printAsMatrix(UString, 3, 3)

print("ORANGE")
printAsMatrix(LString, 3, 3)

print("BLUE")
printAsMatrix(FString, 3, 3)

print("GREEN")
printAsMatrix(BString, 3, 3)

print("RED")
printAsMatrix(RString, 3, 3)

print("WHITE")
printAsMatrix(DString, 3, 3)

solution = kociemba.solve(KociembaString)

commandParser(solution)

##mensaje


screen.lcd_clear()
screen.lcd_display_string("adios", 1)

#cap.release()
cv2.destroyAllWindows()

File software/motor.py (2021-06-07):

from time import sleep
import RPi.GPIO as GPIO

class Motor:
    def __init__(self, directionPin, stepPin):
        self.DIR = directionPin       # Direction GPIO Pin
        self.STEP = stepPin      # Step GPIO Pin
        self.CW = 0         # Clockwise Rotation
        self.CCW = 1        # Counterclockwise Rotation
        self.SPR = 800      # Steps per Revolution (360 / 1.8) * microsteps
        self.DELAY = .005/1 # delay
        GPIO.setmode(GPIO.BCM)
        GPIO.setup(self.DIR, GPIO.OUT)
        GPIO.setup(self.STEP, GPIO.OUT)
        GPIO.output(self.DIR, self.CW)
        #MODE = (14, 15, 18) # Microstep Resolution GPIO Pins
        #GPIO.setup(MODE, GPIO.OUT)
        #RESOLUTION = {'Full': (0, 0, 0),'Half': (1, 0, 0),'1/4': (0, 1, 0),'1/8': (1, 1, 0),'1/16': (0, 0, 1),'1/32': (1, 0, 1)}
        #GPIO.output(MODE, RESOLUTION['1/4'])

    def setDelay(self, delay):
        self.DELAY = delay

    def turn90(self, direction):
        #1 for CCW, 0 for CW
        GPIO.output(self.DIR, direction)
        sleep(.15)
        for x in range(int(self.SPR/4)):
            GPIO.output(self.STEP, GPIO.HIGH)
            sleep(self.DELAY)
            GPIO.output(self.STEP, GPIO.LOW)
            sleep(self.DELAY)

    def turn90CCW(self):
        GPIO.output(self.DIR, self.CCW)
        sleep(.15)
        for x in range(int(self.SPR/4)):
            GPIO.output(self.STEP, GPIO.HIGH)
            sleep(self.DELAY)
            GPIO.output(self.STEP, GPIO.LOW)
            sleep(self.DELAY)
   
    def turn90CW(self):
        GPIO.output(self.DIR, self.CW)
        sleep(.15)
        for x in range(int(self.SPR/4)):
            GPIO.output(self.STEP, GPIO.HIGH)
            sleep(self.DELAY)
            GPIO.output(self.STEP, GPIO.LOW)
            sleep(self.DELAY)

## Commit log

2021-04-02 to print
    [Bearing.SLDPRT, Bearing_spring.SLDPRT, Body12.stl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]
2021-04-02 cad history
2021-04-02 nuevo soporte
    [Body12.stl]
2021-04-03 poste medida correcta
    [Body12.stl]
2021-05-13 motor move
2021-05-14 D motor
2021-05-14 L motor
2021-05-14 two motors
2021-05-17 frame v2
2021-05-19 add jointv1
    [jointv1.stl]
2021-05-19 add antes de corregir joints
2021-05-19 1 motor
2021-05-24 eagle files
    [placa.brd, placa.sch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]
2021-05-28 2nd motor
2021-05-28 back motor]
2021-05-28 one motor
2021-05-28 second motor test
2021-05-28 six motors
2021-05-28 si esto no jala, estoy en problemas
    [testMain.py]
2021-05-28 si esto no jala, estoy en problemas x2
    [testMain.py]
2021-05-29 todo estaba volteado aaaaaaaa
2021-05-29 side correction in scanning phase
    [testMain.py]
2021-05-31 led test
2021-06-01 test con leds
2021-06-02 red abajo de orange en prioridad
2021-06-03 motores con fotos test
2021-06-03 printing colors
2021-06-03 string parser and cube printing
2021-06-03 matrix print fix
2021-06-03 fotos de estados
2021-06-03 green fix ahora si
    [colorCuadrant3.0.py]
2021-06-03 mas pixeles para detectar
2021-06-03 rojo a 8 de nuevo
2021-06-03 un punto en la maskara
2021-06-04 kociembracode correcto por favor funciona pls pls pls pls pls pls plssssssssssssssss
    [colorCuadrant3.0.py]
2021-06-04 unverto quiere que este maaaas lento
